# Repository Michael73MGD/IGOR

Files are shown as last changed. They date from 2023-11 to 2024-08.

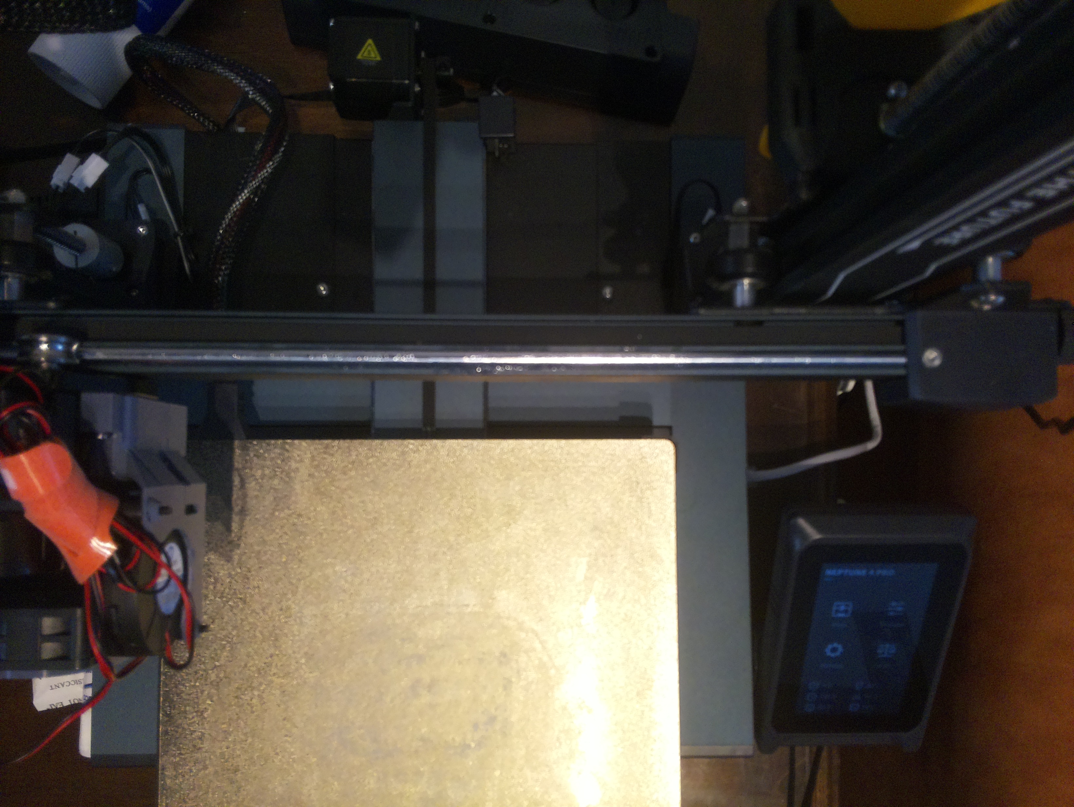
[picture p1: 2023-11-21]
RaspberryPiCode/images/test1.jpg

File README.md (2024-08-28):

# IGOR: Intelligent GO Robot

IGOR is a project focused on bringing an AI-powered coach, teacher, and opponent to the board game Go, which comes from the Japanese word igo, where IGOR gets its name.  

## Motivation
- This project follows in the footsteps of a Hackathon project I participated in a few years ago - a chess-playing robot that I affectionately named [Chester](https://github.com/Michael73MGD/light-blue). Chester was built, programmed, and presented in just 24 hours during a covid-era hackathon in 2021. 

- Go is believed to have been first played over 4,500 years ago in China, and despite its simple rules, it was one of the last board games to be 'conquered' by artifial intelligence; this was done by AlphaGo in 2016. 
- Given its historical significance to humans and AI alike, I believe that Go deserves an AI-powered robot with the crucial ability to interact with a physical game to properly teach human players the rules, strategies, and joys of playing Go. 

## Project Breakdown
IGOR involves several mechanical and programatic projects working in tandem. They are outlined here:

- IGOR the physical robot
    - IGOR is built on the frame of an old 3D printer, allowing 3-axis motion for monitoring and interacting with the game board
    - Stepper motors move IGOR's tool head around the game board where it's camera can get a view of every piece's location, and allows the electromagnetic claw to manipulate stones (game pieces)
    - Custom 3D-printed stones are arranged on a 9x9 game board with embedded 8x3mm magnets, which allow the electromagnet on the tool head to pick up, move, and discard stones
    - The [Raspberry Pi camera module](https://www.raspberrypi.com/products/camera-module-v2/) mounted on the toolhead allows IGOR to view the game board after each human interaction
    - This is connected to a [Raspberry Pi 4](https://www.raspberrypi.com/products/raspberry-pi-4-model-b/) which controls the stepper motors of the robot, analyzes images, and decides IGOR's moves
- IGOR the AI
    - IGOR is also large language model-powered artificial intelligence that can be interacted with using text-to-speech and speech-to-text
    - For this functionality, IGOR the physical robot's Raspberry Pi connects to a locally-run instance of Llama2
    - This AI can control the difficulty level during a match, setup practice scenarios, explain rules and strategies, and offer coaching and encouragement to users, all through voice inputs
- IGOR in its final form
    - Go is an incredibly popular board game, though its high skill ceiling and complicated strategies make it intimidating for new players
    - The goal of IGOR is to successfully introduce Go, explain the rules to new players through physical examples and scenarios, and train them to be a competent player faster than any preprogrammed app, website, or human could hope to achieve. 
    - We've brought superior AI to Go, it's time to upgrade coaches to match and get more people into this historic game

### Task list
- 3D printed 9x9 Go board with divets that allow reliable placement of stones
    - See `STLs/board/full_board_VX.stl`
    - Board was custom designed for this purpose, inlcuding lines between each stone location and rounded divets for them to reliably fall into
- Stones embedded with iron (for the electromaget to attract)
    - [Hex nuts](https://a.co/d/gF2kllP)
        - The hex nut needs to be ferromagnetic (iron/steel) so that it can be picked up and released by the electromagnet
        - 304 Stainless Steel would not work for this purpose, therefore the zinc-plated steel nuts were used
    - See `STLs/board/stone_M6_hole_VX.stl`
    - Stone was designed starting from an online model (`STLs/STL_sources.md`), resized, trimmed, and with a M6 nut-sized hole in it for the hex nut to be placed in
- 3D printed electromagnetic stone mover (5V)
    - Electromagnets:
        - [20x15mm 5V](https://www.aliexpress.us/item/2251832388745731.html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)
        - [10x10mm 6V (selected)](https://www.aliexpress.us/item/2251832637809479.html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,scm-url:1007.40050.362094.0,pvid:083fd9e9-f589-4a9c-b498-bd4fd91a01a6,tpp_buckets:668%232846%238112%231997&pdp_npi=4%40dis%21USD%212.50%211.97%21%21%212.50%21%21%402103011017002704501335673efcc1%2164932969706%21rec%21US%212673377647%21)
    - Microphone / speaker
        - Bluetooth speaker should suffice
- 3D printed camera mount
    - Requirements:
        - Needs to be easily mounted/dismounted
        - Fits Raspberry Pi camera V2.1
        - Needs a good view of the game board
    - Solution: `STLs/raspi/picase_dovetail.stl`, `dove19.6.stl`, `picamcap.stl`
        - The Pi case is modified to mount onto the aluminum extrusions on the top of my 3D printer, and provides a dovetail mount at the front for the camera to slide onto
        - The camera mount is modified to slot into the dovetail and provide an ideal view of the printer bed

- 3D printed stone hopper
    - Requirements:
        - Needs to allow automatic feeding of stones to the electromagnet
        - Gravity driven, mounted to the side of the unit
        - Electromagnet moves to a position above the next stone and lifts it up, allowing the next to fall into place
        - Magnets in the stones cannot interfere, need to store them side to side
    - Custom designed from scratch to match needs and fit custom game stones
        - `STLs/Hopper/hopper_VX.stl`
        - Mounting solution will likely attach to the right side x-axis 
- Python programming running on the Raspberry Pi
    - Stone moving controls
    - Image capture controls
    - Image analysis
    - Go AI (non LLM)
    - Speech to text
    - Text to speech
- LLM run on a desktop
    - API connection to Raspberry Pi for sending/receiving LLM instructions
    - Ability to control Go AI difficulty
    - Ability to run a tutorial session
    - Ability to set up and explain practice scenarios
    - Stretch goals:
        - AI image generator - possibly pixel graphics. Generate an avatar for each difficulty, can regenerate each time
        - After every move, assess situation and generate an image along with a text response 
        - Model after a pixel graphics game with speech bubbles

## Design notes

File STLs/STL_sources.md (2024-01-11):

[Pi cam mount](https://www.printables.com/model/136083-pi-camera-enclosure-mix/files)

[Raspberry Pi 4 Case](https://www.printables.com/model/174099-raspberry-pi-4-case)

[Go board/stone starting point](https://www.thingiverse.com/thing:4676299)

[Hopper x-axis mount](https://www.printables.com/model/630948-elegoo-neptune-4-series-webcam-camera-mount-c270)

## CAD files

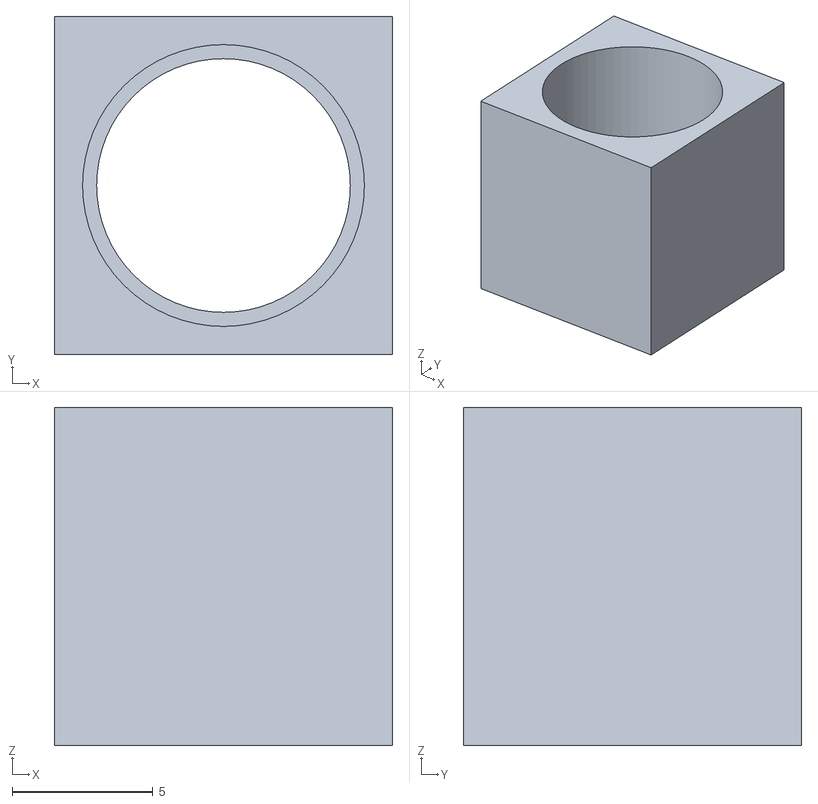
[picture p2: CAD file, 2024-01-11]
STLs/electromagnet/electromagnet_holderV1.stl
12.0 x 12.0 x 12.0

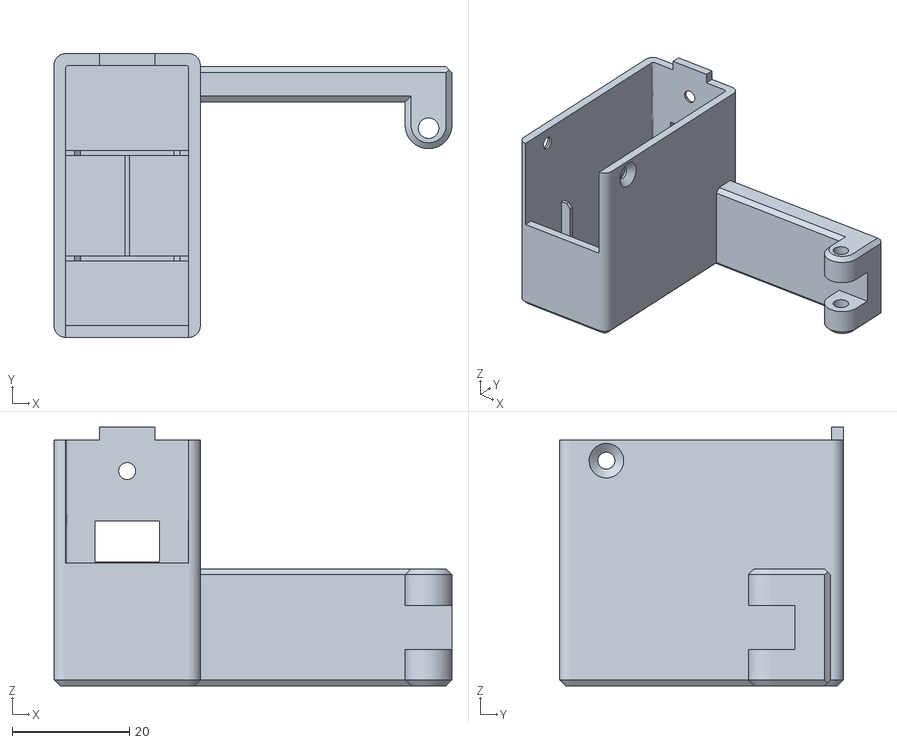
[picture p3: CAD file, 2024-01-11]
STLs/Hopper/N4M Webcam Mount X.stl
68.0 x 48.5 x 44.2

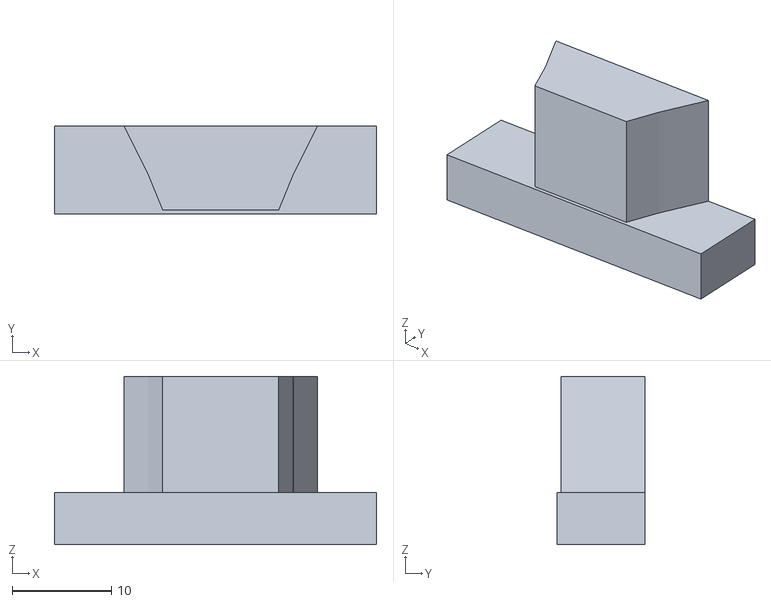
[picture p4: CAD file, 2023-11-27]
STLs/raspi/dove19.5.stl
32.5 x 8.86 x 17.0

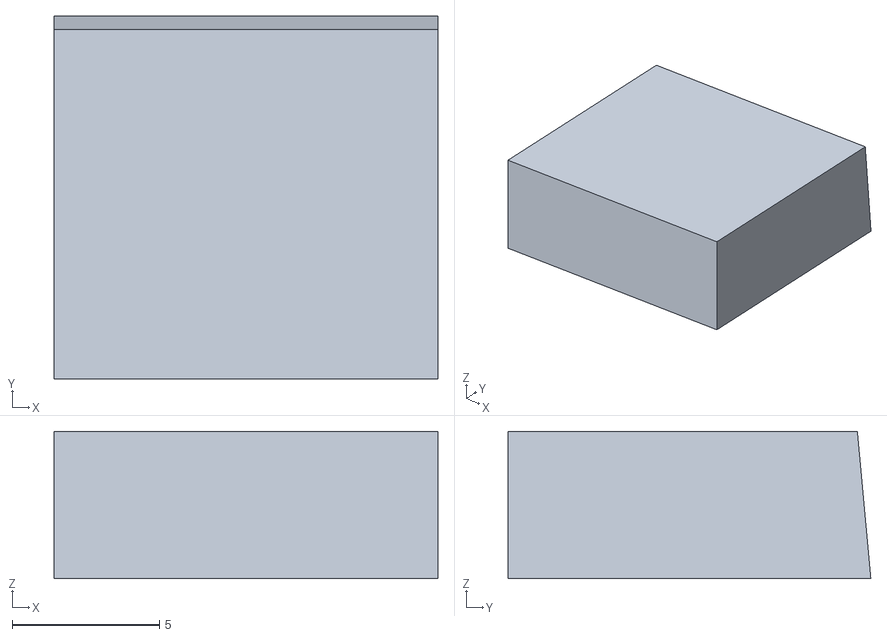
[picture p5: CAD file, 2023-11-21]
STLs/temp/embedded_magnet.stl
13.0 x 12.3 x 5.00

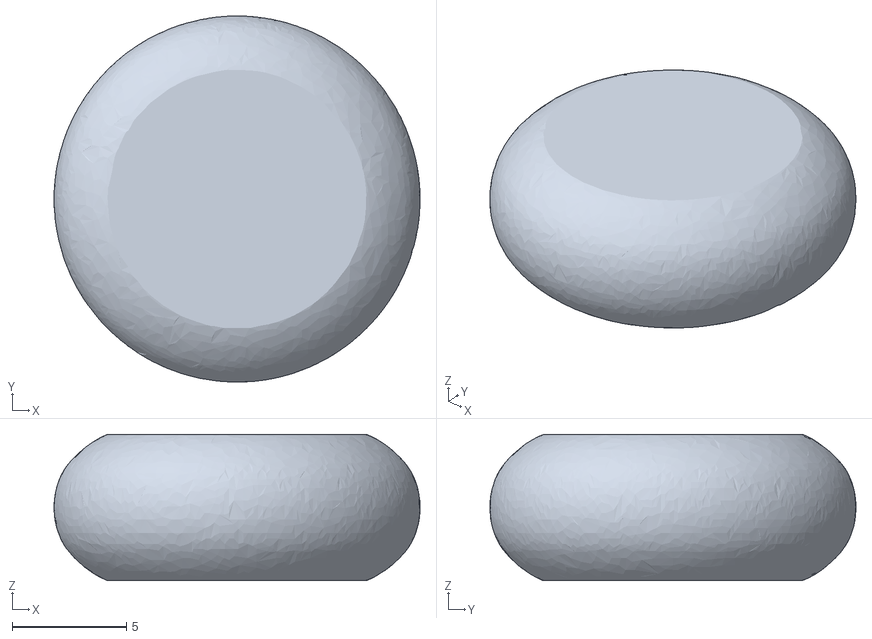
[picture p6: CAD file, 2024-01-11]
STLs/board/trimmed_stone_5mmhexhole.stl
16.0 x 16.0 x 6.40

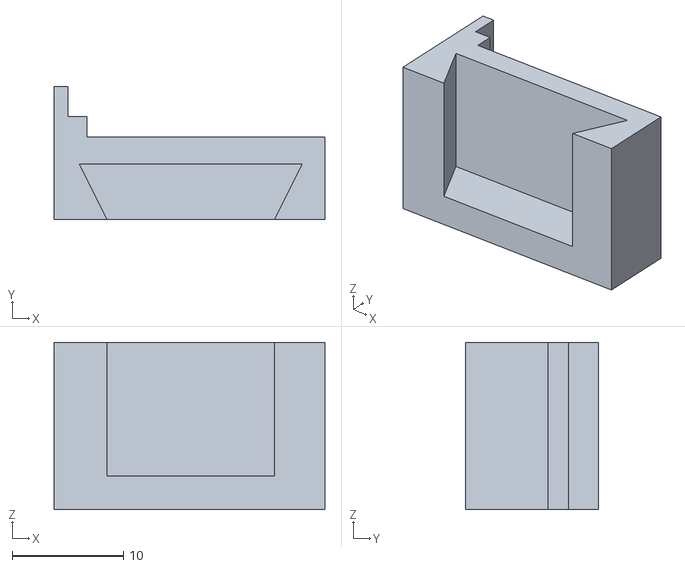
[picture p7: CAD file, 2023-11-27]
STLs/raspi/dovetailtester.stl
24.3 x 11.9 x 15.0

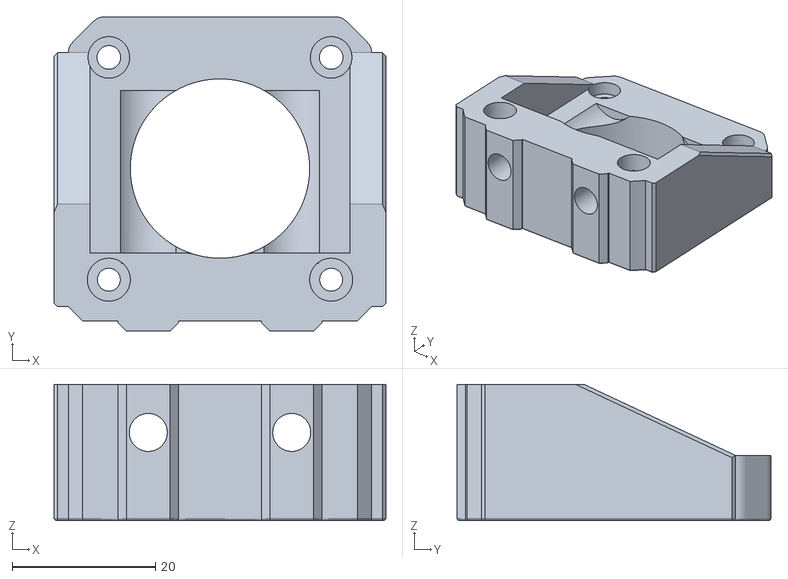
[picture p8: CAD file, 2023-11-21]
STLs/temp/Z-Stepper Mount short version.stl
46.3 x 43.8 x 19.0

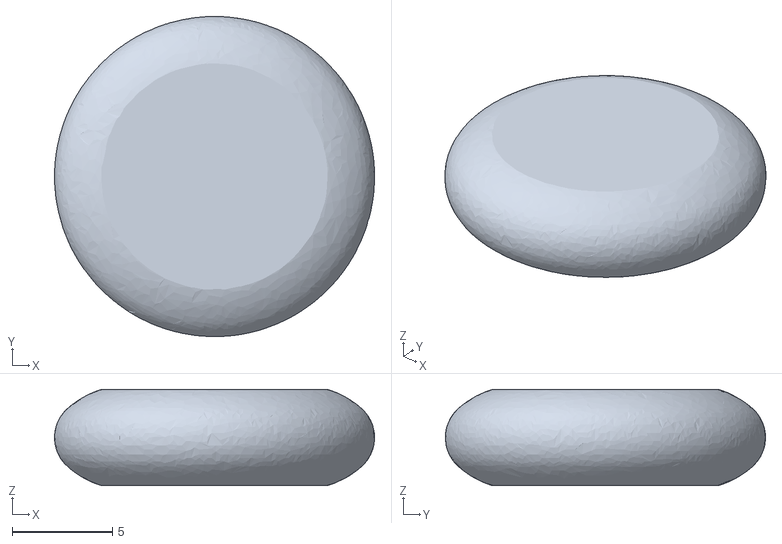
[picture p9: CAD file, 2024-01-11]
STLs/board/trimmed_stone_3.2hexhole.stl
16.0 x 16.0 x 4.80

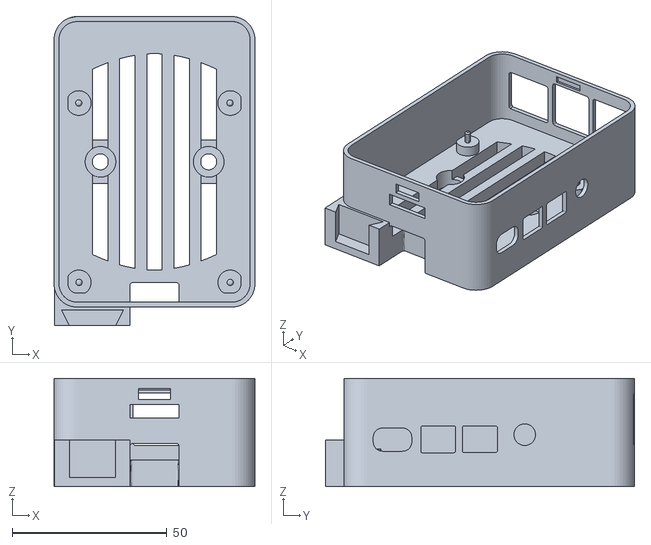
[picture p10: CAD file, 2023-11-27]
STLs/raspi/picase_dovetail.stl
65.0 x 99.9 x 35.0

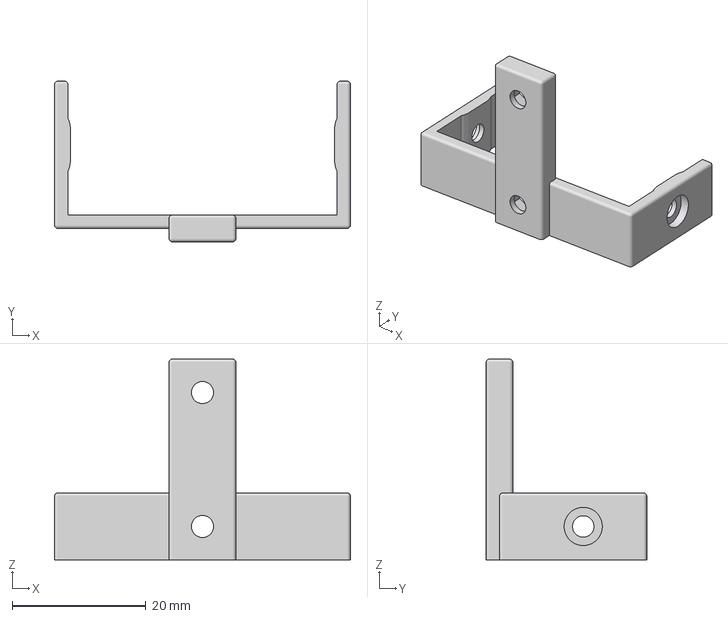
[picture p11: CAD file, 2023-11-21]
STLs/temp/raspi-case-4020-bracket-hexnuts.3mf
44.2 x 24.0 x 30.0 mm

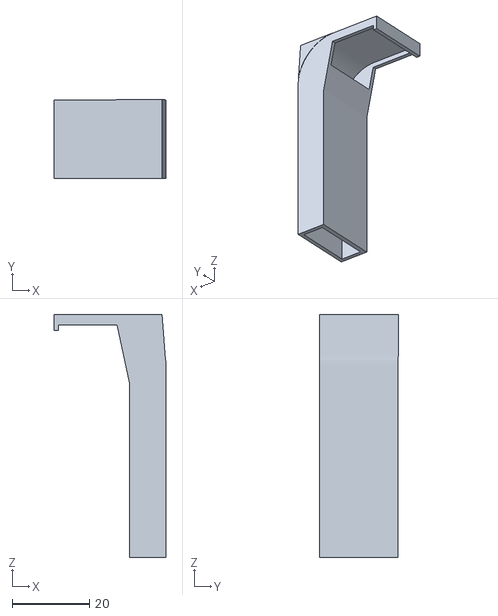
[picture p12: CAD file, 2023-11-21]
STLs/Hopper/hopper_V4.stl
29.0 x 20.5 x 63.0

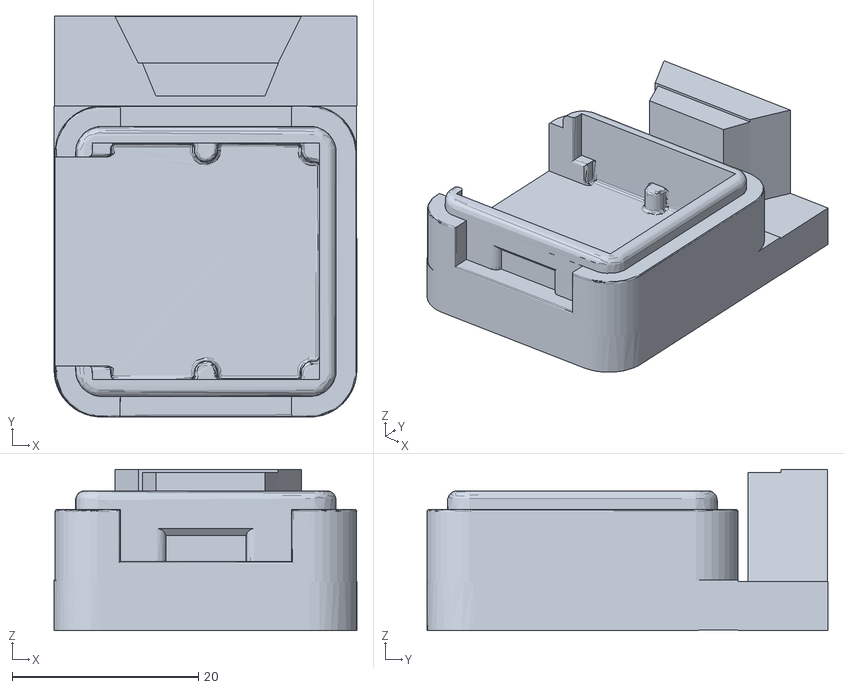
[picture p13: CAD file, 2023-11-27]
STLs/raspi/dovetail2.stl
32.5 x 43.0 x 17.3

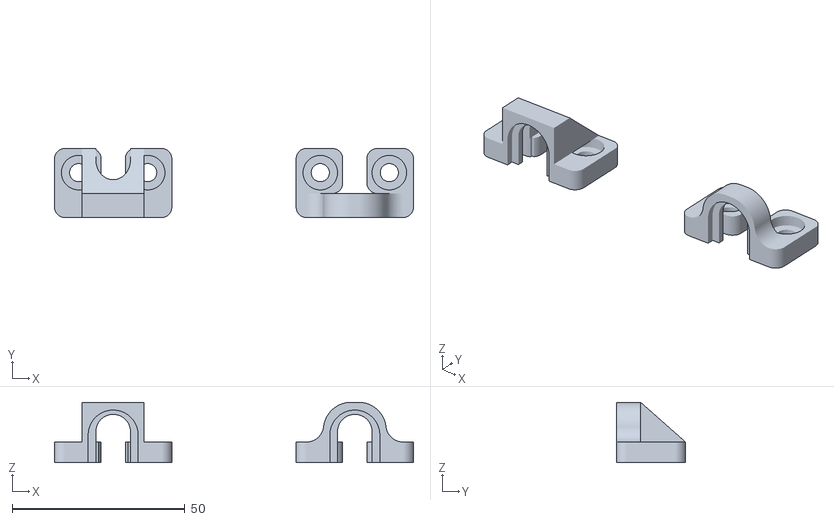
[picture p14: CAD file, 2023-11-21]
STLs/temp/cable_grommet_mount.stl
104.0 x 20.0 x 17.5

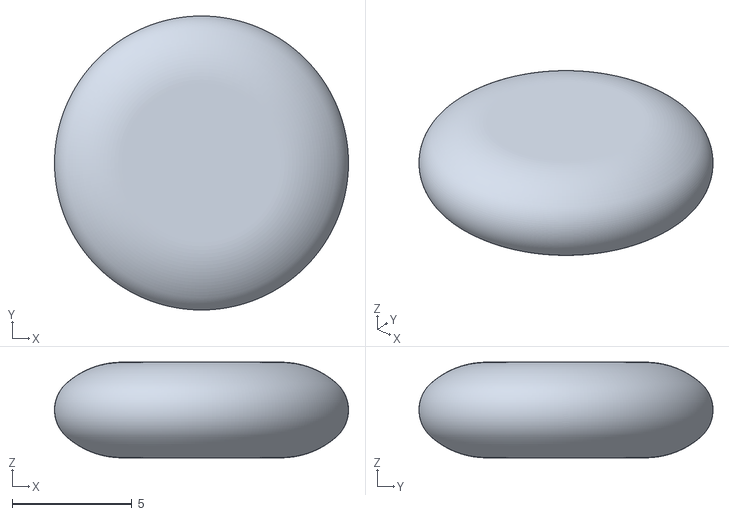
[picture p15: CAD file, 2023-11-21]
STLs/board/piece_no_nub.stl
12.3 x 12.3 x 4.00

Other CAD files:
STLs/board/stone_M6_hole_V1.stl
STLs/raspi/dovetail23.stl
STLs/board/v1test.stl
STLs/raspi/dove19.6.stl
STLs/Hopper/N4M Webcam Mount X.f3d
STLs/Hopper/hopper_V1.stl
STLs/Hopper/hopper_V2.stl
STLs/Hopper/hopper_V3.stl
STLs/board/stone_with_nut_hole.stl
STLs/board/stonetest.stl
STLs/board/v1.stl
STLs/board/v2test.stl
STLs/raspi/CASE.3mf
STLs/raspi/CASE.stl
STLs/raspi/Pi_Camera_Mount.stl
STLs/raspi/Pi_Camera_Mount_more_clip.stl
STLs/raspi/Sizzling Duup-Densor.stl
STLs/raspi/cam_back.stl
STLs/raspi/cam_front.stl
STLs/raspi/picamcap.stl
STLs/raspi/picamclipon.stl
STLs/raspi/picaseclipon.stl
STLs/raspi/raspicamcover_nolense.stl
STLs/raspi/top.3mf
STLs/raspi/top.stl

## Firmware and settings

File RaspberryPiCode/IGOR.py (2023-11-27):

import serial   #Confusingly, the package for this is pySerial not serial
import time
import sys
import paramiko
import urllib
import cv2 as cv
# from cv_cmds import take_picture, crop_quadrant, get_centroid, get_contours, extract_HSV_channels
import numpy as np
import signal
import math
import io
from picamera import PiCamera


ser = serial.Serial('/dev/ttyACM1', 115200)
ser.write(b'G28 X0\r\n')

ser.close()


def camera_test():
    camera = PiCamera()
    camera.resolution = (2592, 1944)
    camera.capture('./image.jpg')


# raspistill -o Desktop/image.jpg
# libcamera-still -o test.jpg
# scp pi@raspberrypi:test.jpg .

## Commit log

2023-11-20 Basic setup and test code
    [Pi_Camera_Mount.stl, Pi_Camera_Mount_more_clip.stl, cam_back.stl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]
2023-11-21 test code and stl progress
    [CASE.3mf, CASE.stl, Sizzling Duup-Densor.stl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]
2023-11-27 improved pi mount and camera location
    [dove19.5.stl, dove19.6.stl, dovetail2.stl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]
2024-01-11 Reorganization, new files and parts
    [CASE.3mf, CASE.stl, N4M Webcam Mount X.f3d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]
